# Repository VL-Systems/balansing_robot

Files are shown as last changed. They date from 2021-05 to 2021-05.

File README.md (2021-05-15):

# Балансирующий робот. Версия 2

Ранее я уже собирал балансирующего робота, но делал это с помощью двух двигателей постоянного тока, в этот раз я хотел использовать шаговые двигатели, что бы лучше разобраться с их принципом работы. Репозиторий возможно будет дополняться и обрастать новыми программами и материалом. 
Видео о данном роботе можно посмотреть по ссылке:

## Структура проекта:
- balansing_robot: папка в которой храняться самые акутальные программы в которых все уже настроено и работает
- body: 3D модель робота, можно использовать для изготовления
- IMU: некоторые полезные программы для работы с IMU датчиком MPU-6050(MPU9250 тоже может использовать эти программы)
- stepper_motor_setup: программа для проверки того как работают шаговые двигатели через Arduino с помощью внутренних таймеров
- image: изображения для статьи
- electronic.pdf электрическая схема проекта

## Общая теория
Ссылка на неплохую статью про балансирующего робота: https://habr.com/ru/post/220989/

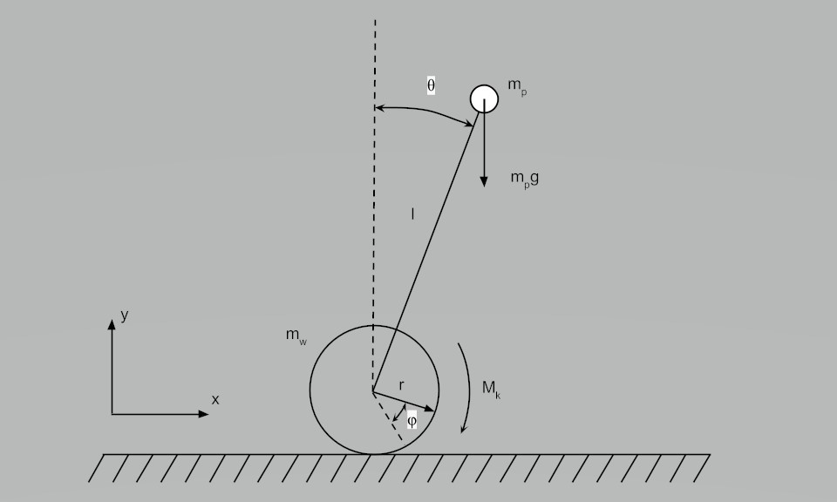
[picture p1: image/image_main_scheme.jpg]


Выше приведена кинематическая схема балансирующего робота
Еще схему такого робота называют "обратный маятник", думаю не сложно догадаться почему
Здесь есть 1 важное допущение, что мы принебрегаем массой робота и считаем, что вся масса робота сосредоточена сверху, что на самом деле не так.
Вся масса робота распределена по корпусу и если мы хотим учитывать все массы и их смещения, то это потянет как минимум на неплохую научную работу. 

Здесь нас интересует больше практическая часть данного робота и вот какие выводы я сделал при сборке данной модели:
1. Необходимо все тяжелые элементы робота смещать вниз, ближе к колесам, сверху ставим наиболее легкие элементы
2. Корпус делаем как можно более легким но жестким, везде где можно экономим массу
3. IMU датчик ставим как можно выше, но таким образом чтобы он распологался на центральной оси робота
4. Если робот уже получился тяжелым, особого смысла ставить на него более сильные шаговые двигатели нет, так как масса увеличится пропорционально мощности
5. Не стараемся перегружать преобразователи напряжения, лучше поставить 2, но чтобы каждый из них работал на 50% от максимума своей мощности
6. Силовые провода берем толстые, так как потреблемение тока будет ~ 5-7А, 
7. Каждый отдельный шаговый двигатель настроен на ток в 2.5\3А и микрошаг в 16, включены 3 и 6 тумблер на TB6600 
8. Колеса чем больше диаметр - тем лучше, но нужно стараться колеса брать с хорошим контактом к поверхности, но при этом достаточно жесткие, чтобы под массой робота колеса имели минимальную деформацию. 

## Arduino 
Не каждая плата сможет управлять таким роботом, особенно управлять независимо двумя шаговыми двигателями. Есть некоторые библиотеки которые могут это сделать, но с этими библиотеками не конектится IMU датчик, а значит все зря.
Вот список тех плат на которых можно собрать робота балансира:
- Arduino Mega2560 
- Arduino Pro Micro

Для того чтобы лучше понимать, что такое таймеры и какое у них преимущество рекомендую вот эти ресурсы к прочтению: 
- https://habr.com/ru/post/453276/
- https://microkontroller.ru/arduino-projects/rukovodstvo-po-tajmeram-arduino-dlya-nachinayushhih/

Так же держите всегда под рукой, изображение с распиновкой Arduino на которой указаны таймеры: 
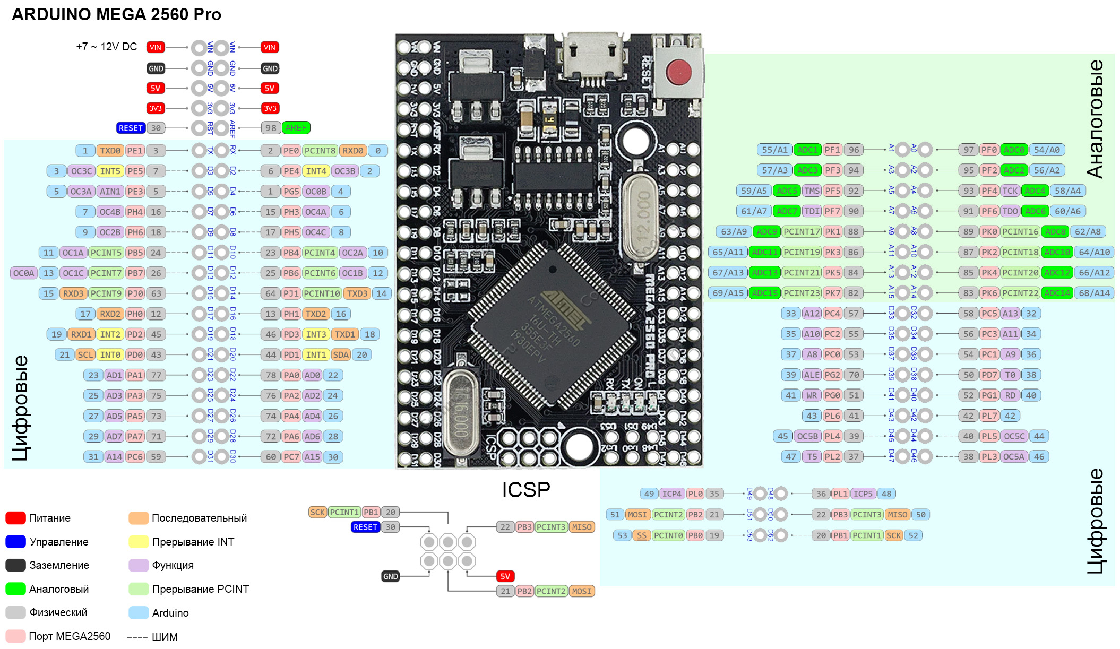
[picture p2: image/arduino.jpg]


А так же карту таймеров в конкретной модели Arduino:
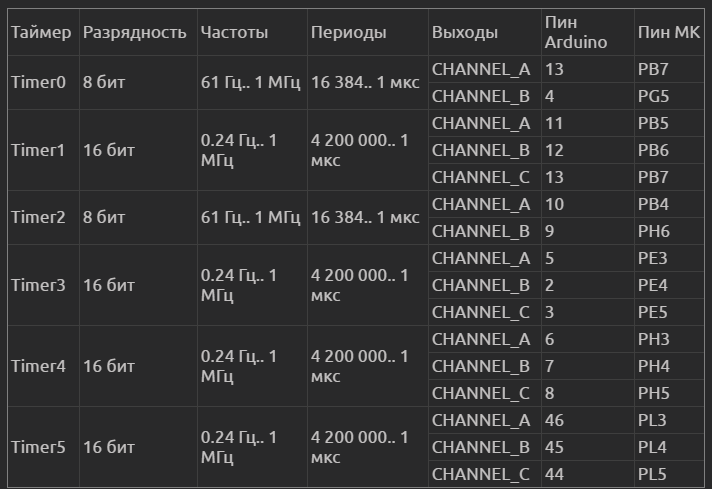
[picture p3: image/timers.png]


## ПИД-регулятора
Настройка ПИД-регулятора ключевой момент на котором было потрачено очень много времени, перед тем как с опишу процесс найстройки программы, стоит сказать о том как устроен ПИД-регулятор, для этого приведу следующую схему: 


В данном проекте используется сразу два ПИД-регулятора
1. Отвечает за установку необходимой скорости движения, будь то нулевая скорость, если робот должен стоять на месте, либо N-скорость для того чтобы робот начал движение
2. Принимает на вход заданный угол отклонения и сравнивает его с текущем углом отклонения, пытаясь минимизировать разницу

С такой системой регулировани уже можно работать, то в моей случае выходной результат от ПИД-регуляторов я отправил в комплементарный фильтр, для того чтобы сделать движение более плавный и убрать мелкую тряску при стабилизации.

### Настройка ПИД-регулятора Методом Циглера-Никольса.
- Для начала обнуляем все коэффициенты регулятора (пропорциональный, интегральный и дифференциальный)
- Постепенно начинаем увеличивать пропорциональный коэффициент и следим за реакцией системы. При определенном значении возникнут незатухающие колебания регулируемой величины.
- Фиксируем коэффициент  KK, при котором это произошло. Кроме того, замеряем период колебаний системы TT.

Собственно, на этом практическая часть метода заканчивается. Из полученного коэффициента KK рассчитываем пропорциональный коэффициент ПИД-регулятора:

#### K_p = 0.6*K

А из него получаем и остальные:

#### K_i = (2*K_p)/T
#### K_d = (K_p*T)/8

Метод довольно прост, но применить его можно далеко не всегда.

### Что делать, если метод Циглера-Никольса не сработал?

Опять же обнуляем все коэффициенты и начинаем увеличивать пропорциональный. Но теперь не ждем появления колебаний, а просто фиксируем поведение системы для каждого значения коэффициента (отличным вариантом будет построение графика величины, которую необходимо стабилизировать, для каждого значения коэффициента). Если видим, что, например, система очень медленно выходит на нужное значение, увеличиваем пропорциональный коэффициент. Система начинает сильно колебаться относительно нужной величины? Значит, коэффициент слишком велик, уменьшаем и переходим к настройке других составляющих.

Понимая, как работает ПИД-регулятор в целом, и представляя, как должна работать настраиваемая система, можно довольно-таки быстро и точно настроить коэффициенты регулятора. Особенно, если есть возможность построить графические зависимости и визуально следить за поведением системы.

Вот некоторые правила, которые могут помочь при настройке ПИД-регулятора:

- Увеличение пропорционального коэффициента приводит к увеличению быстродействия, но снижение устойчивости системы.
- Увеличение дифференциальной составляющей также приводит к значительному увеличению быстродействия.
- Дифференциальная составляющая призвана устранить затухающие колебания, возникающие при использовании только пропорциональной составляющей.
- Интегральная составляющая должна устранять остаточное рассогласование системы при настроенных пропорциональной и дифференциальной составляющих.

Кстати, стоит добавить, что не всегда необходимо использовать все три составляющие ПИД-регулятора, порой хватает пропорциональной и дифференциальной, например (ПД-регулятор). В общем, все сводится к тому, что для каждой системы необходим свой собственный подход при настройке и использовании ПИД-регулятора.

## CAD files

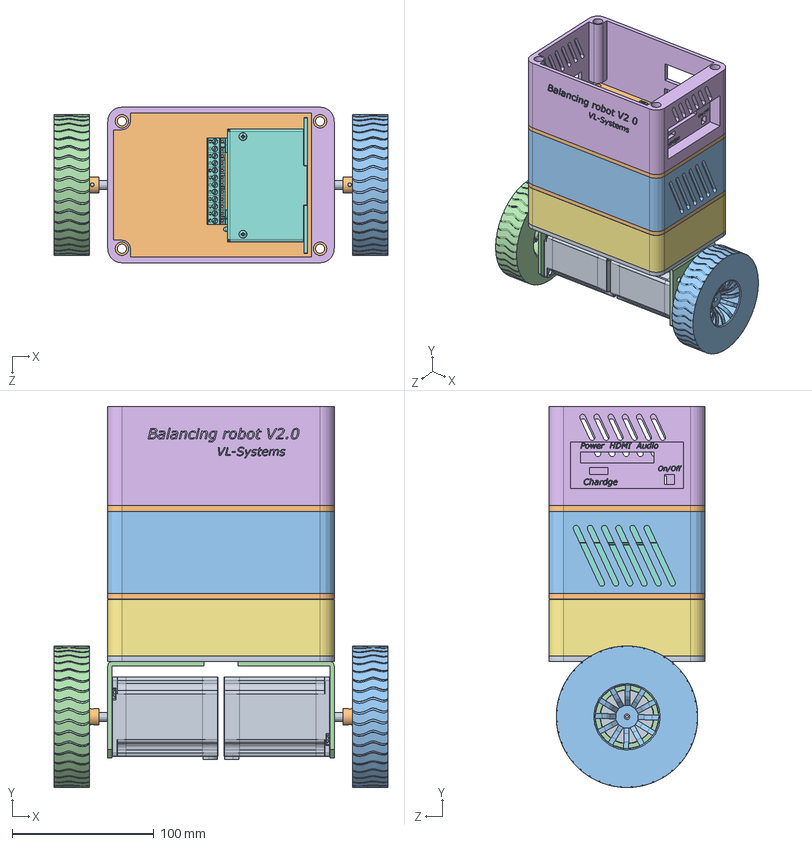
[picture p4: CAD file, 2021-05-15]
body/Сборка_Балансира.SLDASM
235.6 x 269.1 x 110.0 mm
Нижнее основание
Середина x 2
Стенка
Уголок Шагового Двигателя Nema23 x 2
Крепление аккумулятора
Стенка Raspberry
Стенка Аккум
TB6600 Драйвер шагового двигателя x 2
Stepper motor NEMA 23HS7430 x 2
Втулка 8mm x 2
КолесоD100
Зеркально отразитьКолесоD100

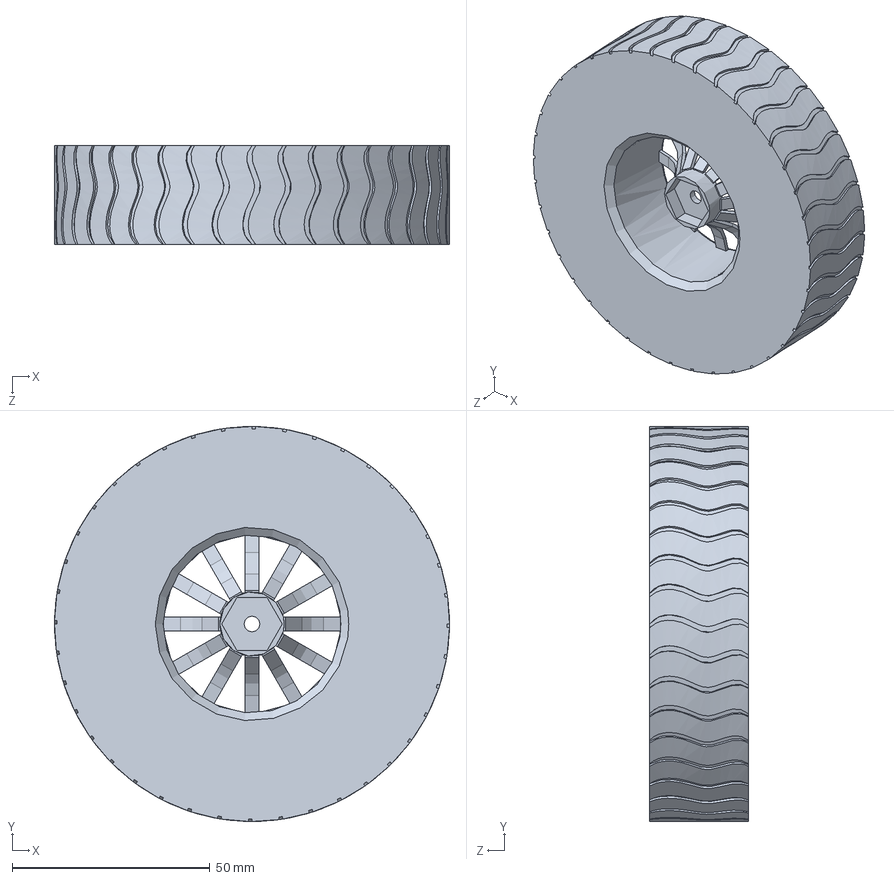
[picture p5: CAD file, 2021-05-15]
body/Зеркально отразитьКолесоD100.SLDPRT
100.0 x 100.0 x 25.0 mm

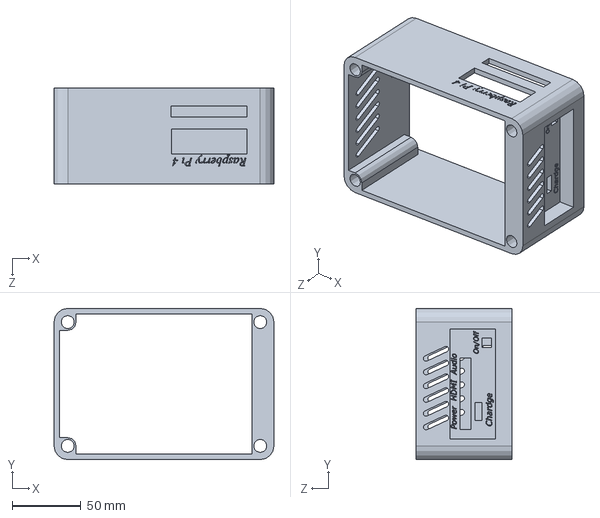
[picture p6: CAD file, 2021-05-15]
body/Стенка Raspberry.SLDPRT
160.0 x 110.0 x 70.0 mm

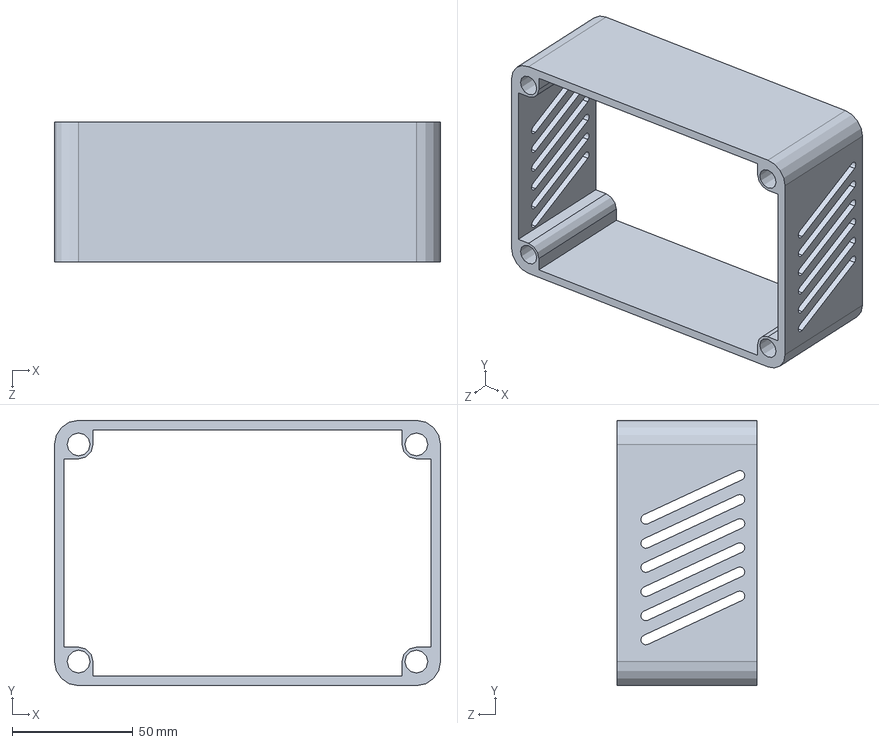
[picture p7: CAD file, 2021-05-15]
body/Стенка.SLDPRT
160.0 x 110.0 x 58.0 mm

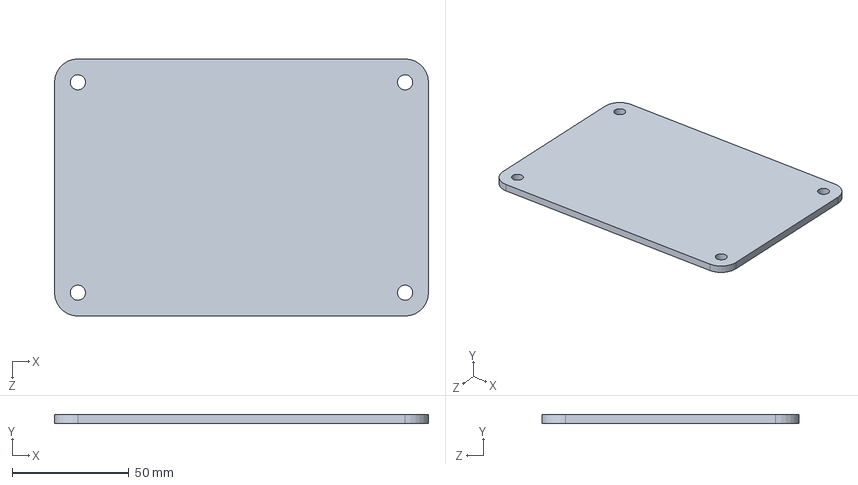
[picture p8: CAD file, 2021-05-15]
body/Середина.SLDPRT
160.0 x 4.00 x 110.0 mm

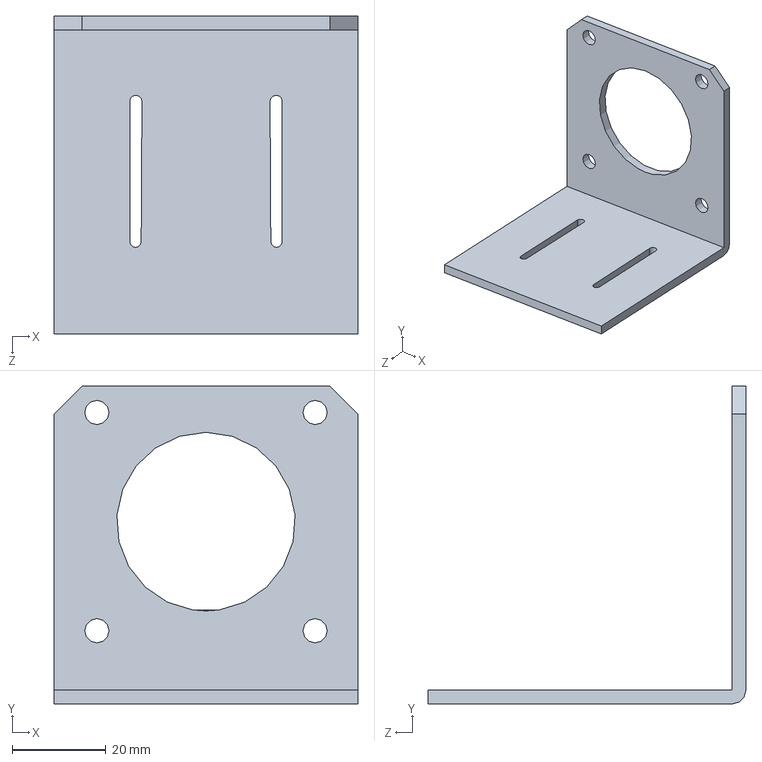
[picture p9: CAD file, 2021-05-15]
body/Уголок Шагового Двигателя Nema23.SLDPRT
65.0 x 68.0 x 68.0 mm

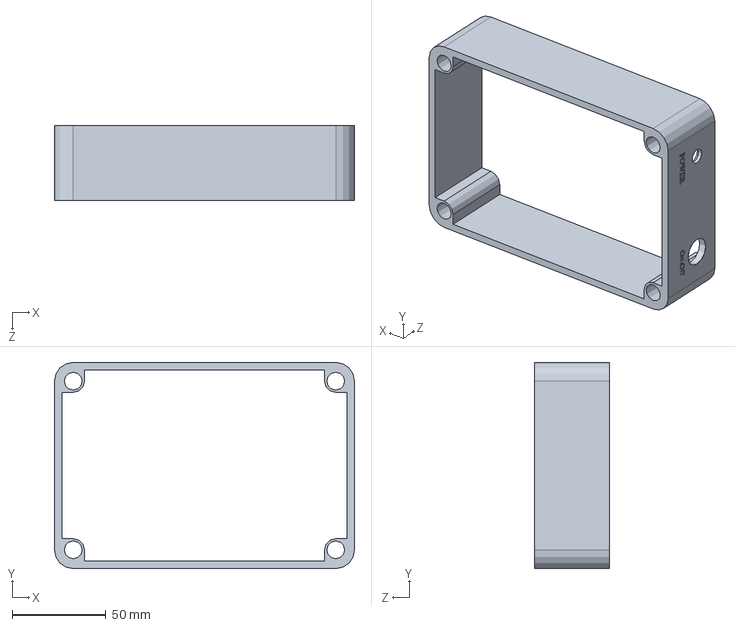
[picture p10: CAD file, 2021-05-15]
body/Стенка Аккум.SLDPRT
160.0 x 110.0 x 40.0 mm

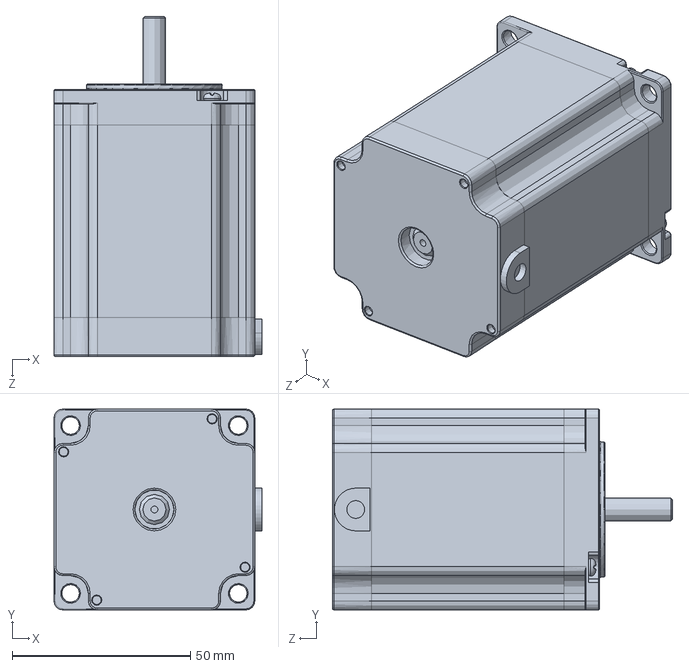
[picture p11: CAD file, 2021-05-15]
body/Stepper motor NEMA 23HS7430.SLDPRT
58.4 x 56.4 x 95.6 mm

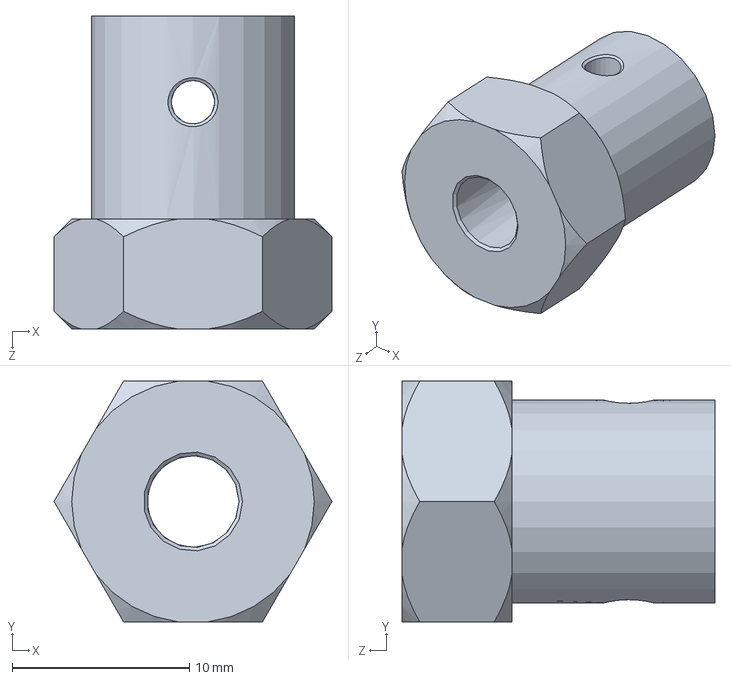
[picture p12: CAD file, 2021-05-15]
body/Втулка 8mm.SLDPRT
15.7 x 13.6 x 17.7 mm

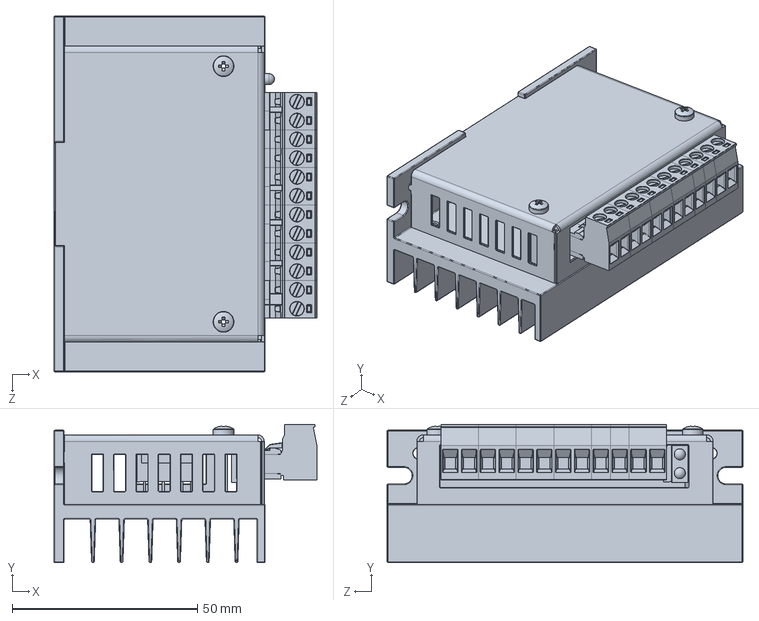
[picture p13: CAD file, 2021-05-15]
body/TB6600 Драйвер шагового двигателя.SLDPRT
71.0 x 37.4 x 96.0 mm

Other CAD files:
body/КолесоD100.SLDPRT
body/Нижнее основание.SLDPRT

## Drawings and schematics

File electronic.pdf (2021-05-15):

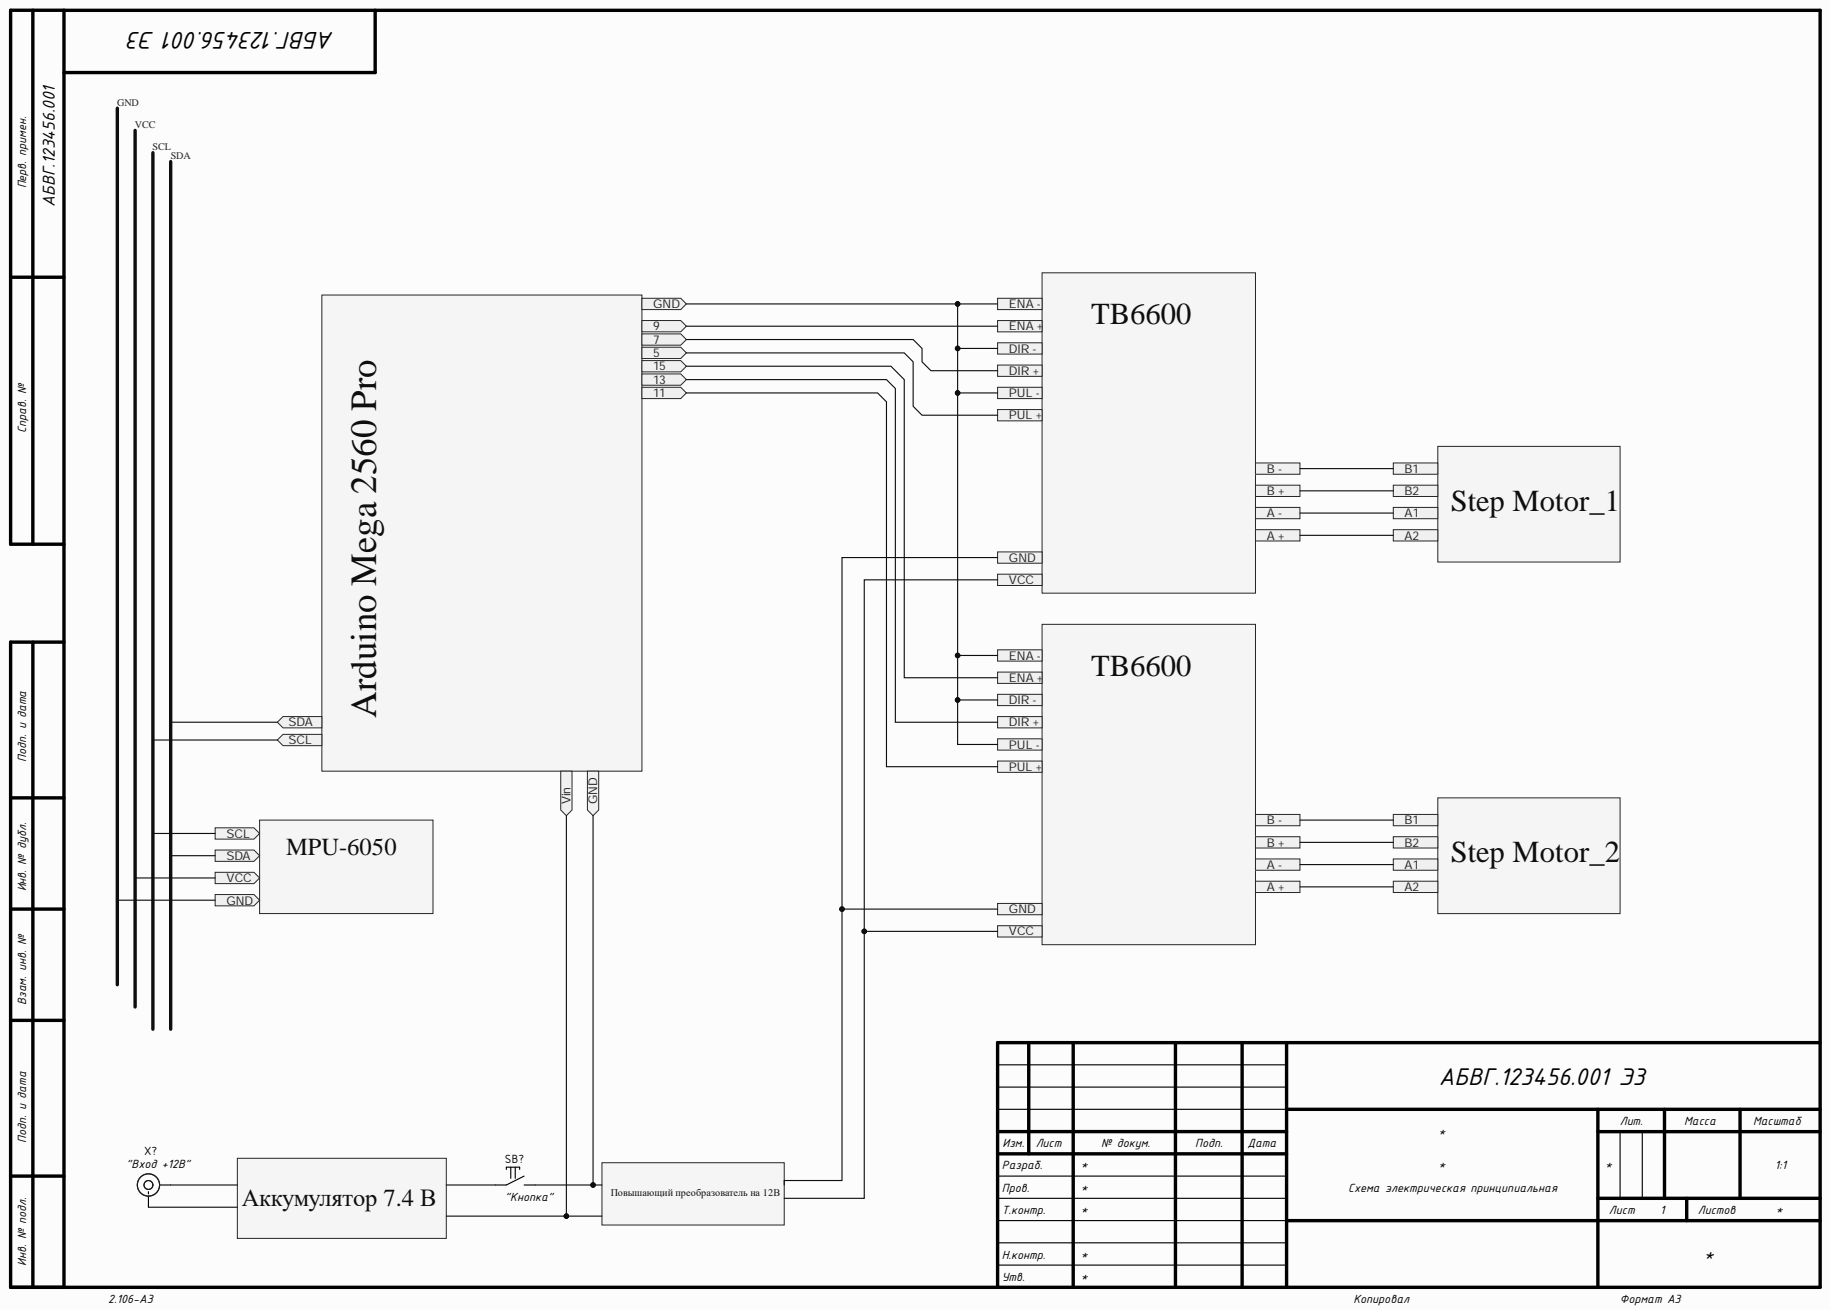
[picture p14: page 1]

Подп. и дата Перв. примен. Справ. №

Инв. № подл. Инв. № дубл. Подп. и дата Взам. инв. №

АБВГ.123456.001 Э3

* * Схема электрическая принципиальная | Лит. | Масса | Масштаб

Изм. | Лист | № докум. | Подп. | Дата | | * | | | 1:1

Разраб. | | *

Пров. | | *

Т.контр. | * | | | | Лист 1 | Листов *

Н.контр. | *

Утв. | *

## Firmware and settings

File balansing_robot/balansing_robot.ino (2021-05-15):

//Подключаем библиотеки и файлы из текущей папки
#include "mpu6050.h"
#include "complementaryFilter.h"
#include "pinConfig.h"
#include "config.h"
#include <Wire.h>
#include "pid.h"

//Вызов IMU датчика
Mpu6050 imu = Mpu6050(MPU6050_ADDRESS);
//Вызов комплиментарного фильтра
ComplementaryFilter angleFilter; 

//Вызов ПИД регулятора для скорости
Pid pid_a(Kp_a, Ki_a, Kd_a,limit_a);
//Вызов ПИД регулятора для угла
Pid pid_s(Kp_s, Ki_s, Kd_s,limit_s);
//Вызов ПИД регулятора для нулевого положения
Pid pid_p(Kp_p, Ki_p, Kd_p, limit_p);

int t=0;
float zero=-2.3;//Смещение нулевого угла из за неидеальности робота, вводиться индивидуально
float targetAngle = 0;//Желаемый угол 
float currentLeanAngle = 0.0f;//Текущий угол
int8_t directionMotor1 = 0;//Направление мотора 1
int8_t directionMotor2 = 0;//Направление мотора 2
int targetSpeed = 0;//Желаемая линейная скорость 
int motorSpeed = 0;//Текущая линейная скорость
int turningSpeed = 0; //Желаемая угловая скорость
float targetPosition = 0; //Желаемое положение    
float currentPosition = 0; //Текущее положение 
boolean balancing = false; //Статус балансировки


void setup() {
  Serial.begin(115200);
  pinMode(STEPPER_1_STEP_PIN, OUTPUT);
  pinMode(STEPPER_1_DIR_PIN, OUTPUT);
  pinMode(STEPPER_2_STEP_PIN, OUTPUT);
  pinMode(STEPPER_2_DIR_PIN, OUTPUT);
  pinMode(led_indicator, OUTPUT);
  
  digitalWrite(led_indicator, LOW);  
    
  digitalWrite(STEPPER_1_ENABLE_PIN, HIGH); // Выключаем мотор 1
  digitalWrite(STEPPER_2_ENABLE_PIN, HIGH); // Выключаем мотор 2

  Wire.begin();                         
  Wire.setClock(400000); 
  imu.init(); 
  imu.calibradeGyro();
  Serial.print("ok");

 // TIMER1 controls motor 1
  TCCR1A = 0;                             // Timer1 CTC mode 4, OCxA,B outputs disconnected
  TCCR1B = (1 << WGM12) | (1 << CS11);    // Prescaler=8, => 2Mhz
  OCR1A = 65535;                          // longest period, motor stopped
  TCNT1 = 0;

  // TIMER3 controls motor 2
  TCCR3A = 0;                             // Timer1 CTC mode 4, OCxA,B outputs disconnected
  TCCR3B = (1 << WGM12) | (1 << CS11);    // Prescaler=8, => 2Mhz
  OCR3A = 65535;                          // longest period, motor stopped
  TCNT3 = 0;

  TIMSK1 |= (1 << OCIE1A);    // Enable TIMER1 interrupt
  TIMSK3 |= (1 << OCIE3A);    // Enable TIMER3 interrupt

}

// TIMER 1: controlling motor 1
ISR(TIMER1_COMPA_vect)
{
  TCNT1 = 0;  
  if (directionMotor1 == 0)
    return;
    
  PORTB |= (1<<PORTB5); //set bit       // same as digitalWrite(STEPPER_1_STEP_PIN, HIGH); 
  delay_05us();
  PORTB &= ~(1<<PORTB5); //clear bit    // same as digitalWrite(STEPPER_1_STEP_PIN, LOW);
}

// TIMER 3: controlling motor 2
ISR(TIMER3_COMPA_vect)
{
  TCNT3 = 0;  
  if (directionMotor2 == 0)
    return;
    
  PORTE |= (1<<PORTE3); //set bit       // same as digitalWrite(STEPPER_2_STEP_PIN, HIGH); 
  delay_05us();
  PORTE &= ~(1<<PORTE3); //clear bit    // same as digitalWrite(STEPPER_2_STEP_PIN, LOW);
}
int new_speed = 0;
float angle = 0;
void loop() {
  imu.updateIMUdata(); 
  // Вычисляем угол отклонения, и передаем его в комплемемнтарный фильтр 
  //float accAngle = atan2(imu.getAccelY(), imu.getAccelX()) * 57;  
  float accAngle = atan(imu.getAccelY()/(sqrt(pow(imu.getAccelX(),2)+pow(imu.getAccelZ(),2))))* 57;   
  angle = angleFilter.calculate(accAngle, imu.getGyroY(), TARGET_DELTA_TIME); 
  currentLeanAngle = angle * 0.7 + currentLeanAngle * (1 - 0.7);
  // вычисляем скорости через 3 пид регулятора 
  //targetSpeed = pid_p.updatePID(targetPosition, currentPosition, TARGET_DELTA_TIME);
  float targetAngle = pid_s.updatePID(targetSpeed, motorSpeed, TARGET_DELTA_TIME)+zero; 
  motorSpeed = -pid_a.updatePID(targetAngle, currentLeanAngle, TARGET_DELTA_TIME);

   new_speed = angleFilter.calculate(accAngle, imu.getGyroX(), TARGET_DELTA_TIME);
    // motor speed is converted from rotation per second to steps per second
    int16_t leftMotorSpeed = motorSpeed;
    int16_t rightMotorSpeed = motorSpeed; 
    setMotorSpeed(leftMotorSpeed, 2);
    setMotorSpeed(rightMotorSpeed, 1);
    digitalWrite(STEPPER_1_ENABLE_PIN, LOW); // Включаем мотор 1
    digitalWrite(STEPPER_2_ENABLE_PIN, LOW); // Включаем мотор 2
  
  
  //Выводим различные параметры для отладки
    Serial.print("currentLeanAngle: ");
    Serial.print(currentLeanAngle);
    Serial.print(" t: ");
    Serial.print(t);
    Serial.print(" targetSpeed: ");
    Serial.print(targetSpeed);
    Serial.print(" targetAngle: ");
    Serial.print(targetAngle);
    Serial.print(" motorSpeed: ");
    Serial.println(motorSpeed);
}

// Функция управления моторами
void setMotorSpeed(int16_t tspeed, int motorID)
{
  long timer_period;
  int16_t motorspeed = tspeed;
  
  if (motorID == 1) {
    if (motorspeed > 0) {
      timer_period = 2000000 / motorspeed; // 2Mhz timer
      directionMotor1 = 1;
      digitalWrite(STEPPER_1_DIR_PIN, LOW);
    } else if (motorspeed < 0) {
      timer_period = 2000000 / -motorspeed;
      directionMotor1 = -1;
      digitalWrite(STEPPER_1_DIR_PIN, HIGH);
    } else {
      timer_period = 65535;
      directionMotor1 = 0;
    }

    if (timer_period > 65535)   // Check for maximun period without overflow
      timer_period = 65535;

    OCR1A = timer_period;  
    if (TCNT1 > OCR1A)    // Check  if we need to reset the timer...
      TCNT1 = 0;
    
  } else if (motorID == 2){
    if (motorspeed > 0) {
      timer_period = 2000000 / motorspeed; // 2Mhz timer
      directionMotor2 = 1;
      digitalWrite(STEPPER_2_DIR_PIN, HIGH);
    } else if (motorspeed < 0) {
      timer_period = 2000000 / -motorspeed;
      directionMotor2 = -1;
      digitalWrite(STEPPER_2_DIR_PIN, LOW);
    } else {
      timer_period = 65535;
      directionMotor2 = 0;
    }

    if (timer_period > 65535)   // Check for maximun period without overflow
      timer_period = 65535;

    OCR3A = timer_period;  
    if (TCNT3 > OCR3A)    // Check  if we need to reset the timer...
      TCNT3 = 0;
  } 
  
}

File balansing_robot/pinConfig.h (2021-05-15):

const int STEPPER_1_STEP_PIN = 5;   
const int STEPPER_1_DIR_PIN = 7; 
const int STEPPER_1_ENABLE_PIN = 9;   
const int STEPPER_2_STEP_PIN = 11;   
const int STEPPER_2_DIR_PIN = 13;    
const int STEPPER_2_ENABLE_PIN = 15; 
const int led_indicator = 31;

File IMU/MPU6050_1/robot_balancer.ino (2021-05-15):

int IN1 = 7; // Input1 подключен к выводу 5 
int IN2 = 6;
int IN3 = 5;
int IN4 = 4;
int ENA = 9;
int ENB = 3;
int i;
void Motor()
{
  pinMode(ENA, OUTPUT);
  pinMode(IN1, OUTPUT);
  pinMode(IN2, OUTPUT);
  pinMode(ENB, OUTPUT);
  pinMode(IN4, OUTPUT);
  pinMode(IN3, OUTPUT);
  
  
  
  analogWrite(ENA, 255);
    analogWrite(ENB, 255);
}
void MinAlfa(){digitalWrite(IN2, HIGH);
  digitalWrite(IN1, LOW);
  digitalWrite(IN4, HIGH);
  digitalWrite(IN3, LOW);
  }
  void MaxAlfa(){
    digitalWrite(IN2, LOW);
  digitalWrite(IN1, HIGH);
  digitalWrite(IN4, LOW);
  digitalWrite(IN3, HIGH);}

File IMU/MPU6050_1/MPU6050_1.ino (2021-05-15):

#include <Wire.h> // подключение библиотеки для I2C 
#include "gyro_accel.h"// подключение библиотеки для гироскопа и акселирометра mpu 6050
// Defining constants
#define dt 20                       // промежуток времени в милисикундах 
#define rad2degree 57.3              // переменная для перевода из радиан в градусы 
#define Filter_gain 0.95             // переменная для фильтра angle = angle_gyro*Filter_gain + angle_accel*(1-Filter_gain)
// *********************************************************************
//    Global Variables
// *********************************************************************
unsigned long t=0; // Переменная времени 
float y=0,angle_x_gyro=0,angle_y_gyro=0,angle_z_gyro=0,angle_x_accel=0,angle_y_accel=0,angle_z_accel=0,angle_x=0,angle_y=0,angle_z=0;
// *********************************************************************
// Основной код 
void setup(){
  Serial.begin(115200);//Общение с компьютером при 115200
  Wire.begin();// Налало работы с I2C шиной , в (адресс устройства  ), если не назван адресс , то плата подключается к шина  как  мастер  
  MPU6050_ResetWake();// Сбрасывает настройки по умолчанию 
  MPU6050_SetGains(0,1);// Настраивает максимальные значения шкалы измерений гироскопа и акселерометра 
  MPU6050_SetDLPF(0); //Настройка фильтра низких частот 
  MPU6050_OffsetCal();// Каллебровка гироскопа и акселерометра 
  MPU6050_SetDLPF(6); // Настройка фильтра низких частот
  
  
  
  
  
  Serial.print("\tangle_x_accel");
  Serial.print("\tangle_y_accel");
  Serial.print("\tangle_z_accel");
  
  Serial.print("\tangle_x");
  Serial.print("\tangle_y");
  Serial.print("\tangle_z");
  
  Serial.println("\tLoad");

  
    
  t=millis(); 
}
void loop(){
  t=millis(); 
  
  MPU6050_ReadData();
 // Угловая скорость относительно всех осей 
  angle_x_gyro = (gyro_x_scalled*((float)dt/1000)+angle_x);
  angle_y_gyro = (gyro_y_scalled*((float)dt/1000)+angle_y);
  angle_z_gyro = (gyro_z_scalled*((float)dt/1000)+angle_z);
  //Угол поворота относительно всех осей 
  angle_z_accel = atan(accel_z_scalled/(sqrt(accel_y_scalled*accel_y_scalled+accel_x_scalled*accel_x_scalled)))*(float)rad2degree;
  angle_y_accel = -atan(accel_x_scalled/(sqrt(accel_y_scalled*accel_y_scalled+accel_z_scalled*accel_z_scalled)))*(float)rad2degree;
  angle_x_accel = atan(accel_y_scalled/(sqrt(accel_x_scalled*accel_x_scalled+accel_z_scalled*accel_z_scalled)))*(float)rad2degree;
  // Отфильтрованные значения угла поворота относительно всех осей 
  angle_x = Filter_gain*angle_x_gyro+(1-Filter_gain)*angle_x_accel;
  angle_y = Filter_gain*angle_y_gyro+(1-Filter_gain)*angle_y_accel;
  angle_z = Filter_gain*angle_z_gyro+(1-Filter_gain)*angle_z_accel;
  

 


  //Serial.print(angle_x);
 // Serial.print("\t");
  Serial.print(angle_y_accel);
 Serial.print("\t");
  //Serial.print(angle_z);
  //Serial.print("\t");
  
   
 //Вывод оси времени 
  Serial.println(((float)(millis()-t)/(float)dt)*100);

  
  while((millis()-t) < dt){ // Making sure the cycle time is equat to dt
  // Do nothing
  }
  
Motor();
if (angle_y_accel>80&&angle_y_accel<88){MinAlfa();}
else if (angle_y_accel<80&&angle_y_accel>70){MaxAlfa();}
}




  
